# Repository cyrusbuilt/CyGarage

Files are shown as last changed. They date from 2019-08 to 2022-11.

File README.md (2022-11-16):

# CyGarage



Arduino-based (specifically the Adafruit Huzzah ESP8266) IoT garage door opener.

The code in this repository represents the Firmware for the CyGarage IoT garage door opener device, as well as some components for integrating with [OpenHAB2](https://openhab.org).  CyGarage is a [PlatformIO](https://platformio.org/) project and is meant to integrate with an existing garage door opener and provide 2 things: The ability to detect the door's state (open, close, or ajar) and the ability to control the door over HTTP/MQTT. Since there is an [ESP8266](https://www.adafruit.com/product/2471) at the heart of it, that means it is WiFi-enabled and is capable of OTA (Over-the-Air) firmware updates.

## Important Note on Security

CyGarage firmware versions prior to v1.3 had no security built-in and used basic unencrypted HTTP requests for control. There was no SSL (HTTPS) or authentication of any kind. This was a major concern because if someone opened access to the device through their firewall or if a malicious actor were to gain access to the WiFi LAN the device was attached to, being able to open the garage door was trivial. Simply send an HTTP POST to the activation URL and the door opens.  However, starting in v1.3, the default is to use [MQTT](http://mqtt.org/) to pass control messages in JSON format and in turn the device sends status messages in JSON format to MQTT subscribers (such as OpenHAB2). Additionally, these messages are transferred to/from MQTT over TLS using SSL certificates so that the messages are encrypted.  You cannot send control messages to CyGarage directly. You have to publish them to the control channel on the MQTT broker that CyGarage is subscribed to. Additionally, you would need the appropriate certificate and SHA256 fingerprint to connect to and publish the control messages. This security architecture is certainly not infalible, but definitely adds a strong layer of security that was non-existent in previous versions and also provides some means of hardening that security even further (such as using certificates signed by an RSA CA (as opposed to self-signed certs) and using password authentication with the MQTT broker on top of that. You can even configure OpenHAB2 to communicate with the MQTT broker using TLS as well, although this is overkill if the broker is running on the same machine as OpenHAB2 and/or the MQTT standard port is bound to the OpenHAB2 host).

## Theory of Operation

The way this is intended to work is: when the device detects that the door is open or ajar, the user can see this status and (if integrated with OpenHAB or some other similar system) and can get notifications when this occurs. When the device receives the activate command, it then triggers a relay which simulates the garage door button press which will in turn raise or lower the door depending on the current state.  Door activation is essentially "fire-and-forget". It will activate the relay and then assume that the garage door is working. CyGarage then monitors door state using the 2 sensor inputs. It is important to understand this system is not intended to replace the controller inside the garage door opener, but instead *compliments* it by adding state monitoring and remote activation.  Safety checks (something in the path of the door when closing) should still be handled by the garage door opener itself, for example.

## Configuration

The config.h file contains default configuration directives. These options are the hardcoded default values that the system will initially boot with. However, if there is a config.json file present in the root of the SPIFFS file system, then it will override these defaults. Here we'll discuss each option:

- CG_MODEL_2: Comment this line if you are building the firmware for the Model 1 (single door version). By default, this firmare supports Model 2.
- ENABLE_OTA: If you do not wish to support OTA updates, just comment this define.
- ENABLE_MDNS: If you do not wish to support [MDNS](https://tttapa.github.io/ESP8266/Chap08%20-%20mDNS.html), comment this define.
- ENABLE_WEBSERVER: This option is disabled by default for security reasons. Only uncomment this line if you know what you are doing or if you absolutely need it for backward compatibility with older versions of CyGarageMobile.
- CONFIG_FILE_PATH: This is the path to the configuration file. The default is /config.json. The values in this file will override these defaults.
- DEFAULT_SSID: Change this line to reflect the SSID of your WiFi network.
- DEFAULT_PASSWORD: Change this line to reflect the password to your WiFi network.
- WEBSERVER_PORT: If you wish to use a port number other than the standard HTTP port, you can change that here. This option is ignored if ENABLE_WEBSERVER is disabled.
- CLOCK_TIMEZONE: The GMT offset for your timezone (EST [America/New York] is -4 when observing DST. It's -5 when not.)
- SERIAL_BAUD: While it is not recommended, you can change the BAUD rate of the serial port here.
- CHECK_WIFI_INTERVAL: The interval (in milliseconds) to check to make sure the device is still connected to WiFi, and if not attempt to reconnect. Default is 30 seconds.
- CHECK_SENSORS_INTERVAL: The interval (in millisceonds) to check the door contact sensors to determine door state. Default is 3 seconds.
- CLOCK_SYNC_INTERVAL: The interval (in milliseconds) to try to resync the clock with NTP. Default is 1 hour.
- ACTIVATION_DURATION: The amount of time (in milliseconds) to activate the door relay. Default is 2.5 seconds and is recommended this value not be changed unless you have good reason for doing so.
- DEVICE_NAME: This essentially serves as the host name of the device on the network.
- CHECK_MQTT_INTERVAL: The interval (in milliseconds) to check connectivity to the MQTT broker. If the connection is lost, a reconnect will occur. The default value is 35 seconds.
- MQTT_TOPIC_STATUS: The MQTT status topic to publish device status messages to. Default is 'cygarage/status'.
- MQTT_TOPIC_CONTROL: The MQTT control topic to subscribe to for control messages. Default is 'cygarage/control'.
- MQTT_BROKER: The hostname or IP of the MQTT broker.
- MQTT_PORT: The port on the MQTT broker to connect to. The default is 8883 (default port for MQTT over TLS).
- OTA_HOST_PORT: Defines the port to listen for OTA updates on. This option is ignored if ENABLE_OTA is disabled.
- OTA_PASSWORD: The password used to authenticate with the OTA server. This option is ignored if ENABLE_OTA is disabled.
- ip: The default IP address. By default, this devices boots with a static IP configuration. The default IP is 192.168.0.200. You can change that here if you wish.
- gw: The default gateway address. The current default is 192.168.0.1. You can change that here if you wish.
- sm: The subnet mask. By default, it is 255.255.255.0, but you can change that here if need be.

To override the default configuration options, you need to upload a filesystem image containing a file named 'config.json' in the root of the SPIFFS filesystem. The file should like something like this:

```json
{
    "hostname": "CYGARAGE",
    "useDHCP": false,
    "ip": "your_device_ip_here",
    "gateway": "your_gateway_here",
    "subnetMask": "your_subnet_mask_here",
    "wifiSSID": "your_wifi_SSID_here",
    "wifiPassword": "your_wifi_password_here",
    "webserverPort": 80,
    "otaPort": 8266,
    "otaPassword": "your_OTA_password_here",
    "mqttBroker": "your_MQTT_broker_here",
    "mqttPort": 8883,
    "mqttControlChannel": "cygarage/control",
    "mqttStatusChannel": "cygarage/status",
    "mqttUsername": "your_mqtt_username_here",
    "mqttPassword": "your_mqtt_password_here",
    "serverFingerprintPath": "/mqtt.fpn",
    "caCertificatePath": "/ca.crt"
}
```

This configuration file is pretty self explanatory and one is included in the source. The file *MUST* be located in the "data" directory located in the root of the project in order to be picked up by the flash uploader (either via Serial or OTA). Each of the options in the configuration file are self-explanatory and match up with the hard-coded default settings mentioned above. If this file is not present when the firmware boots, a new file will be created and populated with the hardcoded defaults. These defaults can then be changed via the fail-safe menu and saved. You'll notice a couple of additional options in the config.json file not present in config.h. They are as follows:

- mqttUsername: If you have enabled password authentication on your MQTT broker, provide the username here.
- mqttPassword: If you have enabled password authentication on your MQTT broker, provide the password for the username above. If *both* the username and password are provided, then CyGarage will attempt to connect to the broker with the provided credentials; Otherwise, it will attempt to connect without credentials.
- mqttControlChannel: The MQTT control topic to subscribe to in order to receive device commands.
- mqttStatusChannel: The MQTT status topic to publish device status to.
- serverFingerprintPath: The path to the file containing the MQTT broker's SHA256 fingerprint. Default is '/mqtt.fpn'.
- caCertificatePath: The path to the CA certificate that the MQTT broker's certificate was signed with. Default is '/ca.crt'.

If the above values are omitted or invalid, then the system will fail during loadCertificates() and will not be able to connect to MQTT.

## Startup Configuration Sequence

During the boot sequence, configuration defaults are loaded from the directives in config.h. If the config.json file is present at boot, then any configuration values found in there will override the default values in memory.  If no config.json file is found or if it could not be read, then the system will continue using the default values and then generate a new config.json file and populate it with the default values that were loaded. Upon subsequent boots, these values can then be read from config.json and altered by the user. When configuration changes are made from the CLI, the altered values take effect immediately, but are only stored in memory unless the users chooses to save the configuration. Otherwise, all in-memory configuration changes are lost upon reboot (intentionally) so that the user can fallback to a known-good state they entered bad configuration data.

## Getting Started

After you've configured everything the way you need it (as discussed above), build the firmware by either clicking "Build" in the PlatformIO tasks menu, or by opening a terminal to the project directory and typing:

```bash
> platformio run
```

NOTE: The first time you flash the Huzzah, you need to do so over serial (since the OTA code isn't there yet), but subsequent uploads can be done via OTA if configured properly.

The next thing to do is connect the Huzzah to your computer using an FTDI cable like [this one](https://www.adafruit.com/product/70?gclid=EAIaIQobChMIm7-50ZiZ5AIVlIvICh284QPxEAQYBCABEgJkcPD_BwE) and then configure the port in platformio.ini like so:

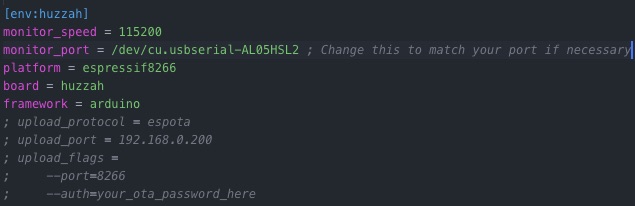
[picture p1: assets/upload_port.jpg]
config


With the above mentioned FTDI cable attached to my MacBook, the port appears as it does in the config file above (usually PlatformIO is pretty good about auto-detecting the port for you).

Now all you have to do is flash the firmware onto the Huzzah. You can do this by first pressing and holding the "GPIO" button and then press the "reset" button and let go of both on the Huzzah to put it into flash mode (this is not necessary when you flash via OTA), then click the "Upload and Monitor" task in the PlatformIO menu or by typing the following into the terminal:

```bash
> platformio run --target upload
> platformio device monitor --baud 115200 --port /dev/cu.usbserial-AL05HSL2
```

Once complete, press the "reset" button on the Huzzah. You should see the device boot up in the serial console. Now put the device back into flash mode. If you are using MQTT over TLS (recommended) then visit the readme in the "openhab" folder (even if you ultimately are not connecting MQTT to OpenHAB) for instructions on generating the necessary files for connecting CyGarage to MQTT, otherwise just click the "Upload File System Image" task in the PlatformIO menu. When finished, press the "reset" button again and the device will reboot and come back up with your new configuration settings.

## Webserver Routes (Deprecated)

These routes are *ONLY* exposed if the ENABLE_WEBSERVER directive is uncommented.

- GET /    (Returns "Server ok..." in plain text)
- GET /version (Returns the firmware version in plain text)
- GET /device/status (Returns the device (door) status in plain text)
- POST /device/activate (Activates the relay and returns "OK" in plain text)

## OTA Updates

If you wish to be able to upload firmware updates Over-the-Air, then besides leaving the ENABLE_OTA option uncommented, you will also need to uncomment all the upload_* lines in platformio.ini, and change the line 'upload_port = ' line to reflect the IP of the device and the line '--auth=' to reflect whatever OTA_PASSWORD is set to. Then when you click "upload" from the PlatformIO tasks (or if you execute 'platformio run --target upload' from the command line) it should upload directly over WiFi and once completed, the device will automatically flash itself and reboot with the new version. If you wish to upload a new configuration file, you can also do this via OTA. Assuming the above-mentioned settings are configured, you can then click "Upload File System Image" from the PlatformIO project tasks.

## Serial Console Menu

If the device ever fails to connect to WiFi or if you press the 'I' key on your keyboard while in the serial console, normal operation of the device is suspended and the device will fall into a 'fail-safe' mode and present the user with a command menu. Here we will discuss those menu options:

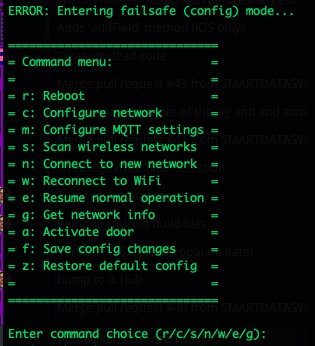
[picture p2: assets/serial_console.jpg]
Console Menu


- Reboot - press 'r' - Self-explanatory. Reboots the device.
- Configure network - press 'c'. Configure the network.

- - Press 'd' for DHCP or 't' for static IP.

- - If static, then you will also be prompted for the IP, gateway, and subnet mask.

- Scan wireless networks - Press 's'. This will scan for available wireless networks and dump a table of the networks it found to the console.

- Connect to new network - Press 'n'. This option prompts the user for a new SSID and password for different WiFi network to connect to.

- Reconnect to WiFi - Press 'w'. This can be used to reconnect to the current WiFi network if the connection was lost.

- Resume normal operation - Press 'e'. This will leave fail-safe mode and attempt to resume normal operation by resuming any suspended tasks and verify network connectivity.

- Get network info - Press 'g'. This will dump network information to the serial console (IP config, WiFi connection info).

- Activate door (1) - Press 'a'. This allows the user to manually activate the door. Activates door 1 on Model 2.

- Activate door 2 - Press 'b'. This allows the user to manually activate door 2. Not present on Model 1 firmware.

- Save config changes - Press 'f'. This will save any configuration changes currently stored in memory to config.json.

- Restore default config - Press 'z'. This will restore the firmware configuration back to the factory default settings (the hard-coded defaults). It does this by simply deleting the existing config.json file from flash storage and then immediately rebooting the firmware. Upon reboot, a new config.json file is created and populated with the default settings which are then applied to the running configuration in memory.

## Dependencies

The firmware dependencies will be installed automatically at compile-time.  However, if you wish to install dependencies prior to compiling (for intellisense or to clear warnings/errors in the VSCode editor) you can run the following command:

```bash
platformio lib install
```

Then go to the platformio menu and click "Rebuild IntelliSense index".

## Tools

Included with this firmware is a few handy tools:

- /disassemble.sh - Disassembles the compiled firmware into a plain text file called 'disassembly.txt'. If the firmware has not been built, it will be compiled first, then disassembled. The disassembly output contains the assembly code, C++ calls, and instruction addresses useful for debugging the executing code or determining the cause of crashes at addresses reported by ESPCrashMonitor during boot.

- tools/clear_flash.sh - Completely clears the flash memory on the ESP8266 of all data (including firmware).

- tools/serial_monitor.sh - Just runs the serial monitor. Pretty much the same as clicking 'Monitor' in the platformio menu, but uses its own settings instead of those found in platformio.ini.

- tools/generate_mqtt_certs.sh - Generates the necessary certificates for the MQTT broker and CyGarage to communicate over TLS.

## Mobile App

If you choose not to integrate with OpenHAB2, you can get similar functionality using the mobile app for iOS and Android located [here](https://github.com/cyrusbuilt/CyGarageMobile). (NOTE: As of 8/21/2019, the most current version of CyGarageMobile is only compatible with CyGarage firmware version prior to v1.3, or if the ENABLE_WEBSERVER option is enabled in v1.3 or higher). If you intend to integrate with OpenHAB2, you can also use the OpenHAB mobile application (recommended).

## Integration with Garage Door opener

Once the board is assembled (either by having the board etched or by just soldering the necessary components to perf board and making the connections manually), you will need to mount the board somewhere and then make the necessary connections to the opener. If using door contacts is not an option for you (which was the case for me), it is possible to use the limit switches already mounted to the track to tell the motor to stop when the door is all the way open or all the way closed. Many garage door openers have voltage present on these limit switches. In the case of my Genie, there was 7.7V DC present when the limit switches were open, which then goes to 0V when the switches closed. We can't have that voltage (or current) being fed back in to the inputs on the ESP8266, so rectifier diodes (D1 and D2) were added to the circuit just before J2 and J3 (respectively). This allows us to use the existing switches, but still isolate the ESP8266 from the garage door opener's voltage and prevent ground loops. That being said, the first thing to do is to locate the terminals on the garage door opener that the wall-mounted push button wires to.

*MOST* garage door openers have a button mounted near the interior door that you can press to open/close the garage door. Follow the wires from that button and see which terminals they wire into on the opener. You need to connect 2 wires from the push button terminals on the opener to the COM and NO screw terminals on the Power Relay FeatherWing (I ran appropriate lengths of 18/2 (18 Guage / 2 lead) for all my connections and mounted the CyGarage board on the wall where I could easily get to it). Next, connect 2 wires each to J2 and J3 and then connect the other ends of each to either magnetic door contacts or the limit switches mounted on the trolley track.  If connecting to the limit switches, it is important to be sure that you are connecting the outside terminals (think of these as the negative or ground terminals) to the frame or ground on the track itself and the inside terminals (think of these as the positive terminals) to the switch leads themselves.

Last, you need to connect a 5VDC 1A power supply to J1. I personally used a power adapter for an old USB hub I still had laying around. But a lot of cell phone chargers and the like would work too, or the 5VDC rail from an old PC power supply, or you could build one, which wouldn't be that difficult. If you intend to mount the board somewhere that will be difficult to hook up to a computer later, it would be best to make sure you flash the ESP8266 with the firmware first. Since mine was mounted on the wall near one of my benches, I just set my laptop on the bench and connect the USB-to-Serial cable and flash it right there (when necessary, I mostly just use the OTA feature). I would HIGHLY recommend that you use female headers to create a sort of 'socket' for the Huzzah. That way it can be replaced if something happens or so you can pop it out and flash it if needed.

For Model 2:

The same as above except J3 and J4 connect to door contacts or limit switches on door 2, and relay 2 connects to the push button terminals on the opener for door 2.

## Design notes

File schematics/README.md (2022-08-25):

# CyGarage Schematics

All files were produced using [EasyEDA](https://easyeda.com/). The following is a list of files and what they are:

- Model1-Single-Door/COM_CyGarage.csv - The bill of materials in CSV format.

- Model1-Single-Door/PCB_CyGarage.pdf - A PDF version of the PCB view.

- Model1-Single-Door/SCH_CyGarage.pdf - A PDF version of the schematic view.

- Model1-Single-Door/PCB_CyGarage.json - The original EasyEDA CAD file of the schematic.

- Model1-Single-Door/SCH_CyGarage.json - The original EasyEDA CAD file of the PCB.

- Model1-Single-Door/gerber - Exported Gerber files useful for importing into other CAD programs or for sending to fab houses that do not support Easy EDA files.

- Model2-Dual-Door/* - Contains all of the same things, but for the 2 door model.

## NOTES

DC1 and DC2 (and DC3 and DC4 for Model2) are actually intended to connect to the limit switches on the garage door track. These are used for sensing door position.

The power supply used is a 5VDC 1A supply which connects to JP1.

When DC1 (connected to JP2) closes, the controller will consider the door to be in the 'open' state. This is the limit switch on the near-end of the trolley track (closest to the opener). When this switch is closed, the garage door opener stops because the door should be fully opened.

When DC2 (connected to JP3) closes the controller will consider the door to be in the 'closed' state (unless DC1 is also closed, which should never happen). This is the limit switch on the far-end of the trolley track (closest to the garage door). When this switch is closed, the garage door opener stops because the door should be fully closed. When both switches are opened, the door is considered to be "ajar".

The OPENER terminals should connect to the button terminals on the garage door opener. When the relay activates, these will be connected for approx. 2.5 seconds and then open again, thus simulating a momentary button press which should in turn activate the garage door opener.

Additionally, I opted to use female stacking headers where the pins of the ESP8266 should go (creating a "socket" of sorts) to allow the module to be removable. This is optional, but handy in the event that the module ever becomes damaged or if the EEPROM wears out, or something of that nature, it can be easily replaced.

DC1 and DC2 (and DC3 and DC4 for Model2) can also be connected to door contacts if using on a garage door that doesn't use limit switches (such as automatic industrial overhead door openers).

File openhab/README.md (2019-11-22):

# OpenHAB Components

This directory contains components for integrating with OpenHAB2.

## Instructions for integrating with OpenHAB2

The first thing you will need to do if you haven't already, is install an MQTT broker. For the purposes of this guide, I will assume you will be using [Mosquitto](https://mosquitto.org/) and will be installing it on the same machine as OpenHAB2.

To install mosquitto, follow the download and install instructions [here](https://mosquitto.org/download/). But assuming you are installing on an Ubuntu or Ubuntu-based system just run:

```bash
> sudo apt-add-repository ppa:mosquitto-dev/mosquitto-ppa
> sudo apt-get update
> sudo apt install mosquitto mosquitto-clients
```

Next we need to generate the necessary SSL certificates that will be used for communication over TLS.  There is a shell script in the tools directory that simplifies this process. Just run:

```bash
> tools/./generate_mqtt_certs.sh
```

You will first be prompted for the hostname and IP address of your MQTT broker (in this example, it is the same as the your OpenHAB2 server). It will also prompt you for some additional information such as country, state/province, Organizational Unit, org name, etc. It will also prompt you for a password. Make note of this password. When the script is finished it will output a bunch of files in tools/certs. As the script indicates, the ones we are most interested in are host_name.key.pem, hostname_.crt.pem, and ca.crt.pem (where host_name is the host name you provided when the tool first ran). These 3 files need to be copied somewhere on your MQTT server. For this example let's assume /etc/mosquitto/certs.

```bash
> sudo mkdir /etc/mosquitto/certs
> sudo cp -f tools/certs/host_name.key.pem /etc/mosquitto/certs
> sudo cp -f tools/certs/host_name.crt.pem /etc/mosquitto/certs
> sudo cp -f tools/certs/ca.crt.pem /etc/mosquitto/certs
```

Next, we need to configure it.

```bash
> sudo nano /etc/mosquitto/mosquitto.conf
```

First make sure the following line is present:

```txt
listener 1883 localhost
```

This binds port 1883 (the default non-SSL port) for MQTT to only allow traffic from the local host.  This is done because encrypting the traffic between OH2 and MQTT when they are running on the same host is overkill, but we also need to make sure that *ONLY* the localhost can do this.  All other traffic will then have to go through another port. In our case, 'all other traffic' will be encrypted traffic. This means we need to define another port and supply the certificates like so:

```txt
listener 1883 localhost

listener 8883
cafile /etc/mosquitto/certs/ca.crt.pem
certfile /etc/mosquitto/certs/host_name.crt.pem
keyfile /etc/mosquitto/certs/host_name.key.pem
```

Press CTRL+X to save and close the file.  Now restart MQTT:

```bash
> sudo systemctl restart mosquitto.service
> sudo systemctl status mosquitto.service
```

It should start back up normally and show the status as active. Now lets test it out:

```bash
> mosquitto_sub -h localhost -p 1883 -t cygarage/status &
> mosquitto_pub -h localhost -p 1883 -t cygarage/status -m "{\"foo\":\"bar\"}"
{"foo":"bar"}
```

You should see the message output. Now you can kill the subscription you created with the first command:

```bash
> fg
```

Now press CTRL+C.

Next, we need to configure OpenHAB to use the MQTT broker. To do this, go to PaperUI -> Addons -> Bindings and install the MQTT Binding.  Once the installation is complete, we need to configure the service:

```bash
> sudo nano /etc/openhab2/services/mqtt.cfg
```

Add the following lines:

```txt
mqtt:localBroker.url=tcp://localhost:1883
mqtt:localBroker.clientId=openhab2
mqtt:localBroker.qos=0
```

Save and close the file.

## Optional password authentication

If you wish to use password authentication with Mosquitto, then there are some additional steps. First, you need to generate the password file.

```bash
> sudo mosquitto_passwd -c /etc/mosquitto/passwd cygarage
```

Where "cygarage" is the username. You can make this whatever you want as long as this same username is what you put in the CyGarage config and in the cygarage.things file. Next, we need to modify the mosquitto config again:

```bash
> sudo nano /etc/mosquitto/mosquitto.conf
```

And add the following lines to the file:

```txt
allow_anonymous false
password_file /etc/mosquitto/passwd
```

Save and close, then restart the service:

```bash
> sudo systemctl restart mosquitto.service
```

Next we need to copy the following files to the openhab-conf folder on the server:

## mqttbridge.things

This is a "Thing" definition for the MQTT bridge. This bridge can be used by anything else in OH2 that needs it. This simply defines a bridge to MQTT that registers OH2 as a client. If a Thing definition for this bridge already exists, no need to copy it again. If not, then copy this file to the openhab-conf/things directory.

## model1/cygarage.things

This is a "Thing" definition for CyGarage that binds the channels we need to MQTT.  You can edit the binding if needed, (such as adding the mosquitto username and password, hostname or IP and port) then copy this file to the openhab-conf/things directory.

## model1/cygarage.items

This file defines the items that will bind to the channels in the cygarage.things file, which will represent controls and display values. Copy this file to your openhab-conf/items folder.

## model1/cygarage.sitemap

This is the sitemap contains all the items defined in the cygarage.items file and makes up all the monitor and control items on one screen. Copy this file to your openhab-conf/sitemaps folder.

## model1/cygarage.rules

Contains automation logic. This file is responsible for sending push notifications if the door is open/ajar for 15 minutes or longer and handles the control actions. Copy this file to your openhab-conf/rules folder.

## model2/*

The same files as above, but to for the Model 2 (2 door version).

## All set

Now that everything is in place. You need to restart OH2:

```bash
> sudo systemctl restart openhab2.service
```

Now lets make sure the service started successfully:

```bash
> sudo systemctl status openhab2.service
```

The service should be active. So let's test it:

```bash
> mosquitto_pub -h localhost -p 1883 -t cygarage/status -m "{\"client_id\":\"test\",\"state\":\"CLOSED\",\"firmwareVersion\":\"1.3\",\"systemState\":0}"
```

Now if you navigate to BasicUI in OH2 and click the CyGarage sitemap, you should see the System ID is "test", Firmware version is "1.3", System State is "Booting 0" and Current position is "CLOSED".

CyGarage Sitemap (Web Version)

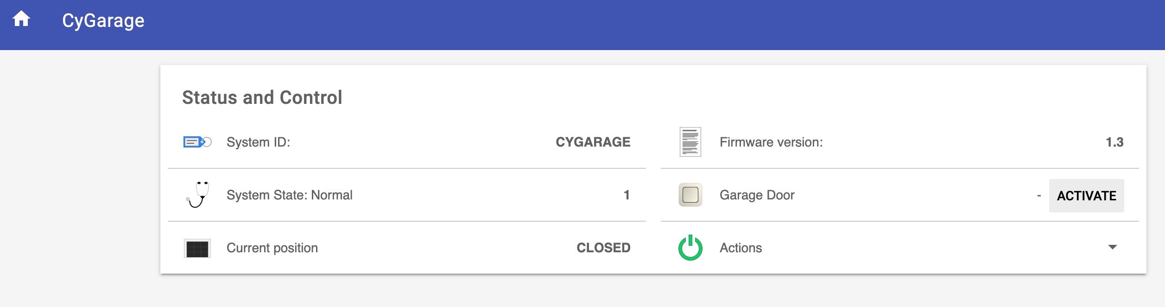
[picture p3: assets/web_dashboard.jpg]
Web Dashboard


CyGarage Sitemap (OH2 Mobile App Version)

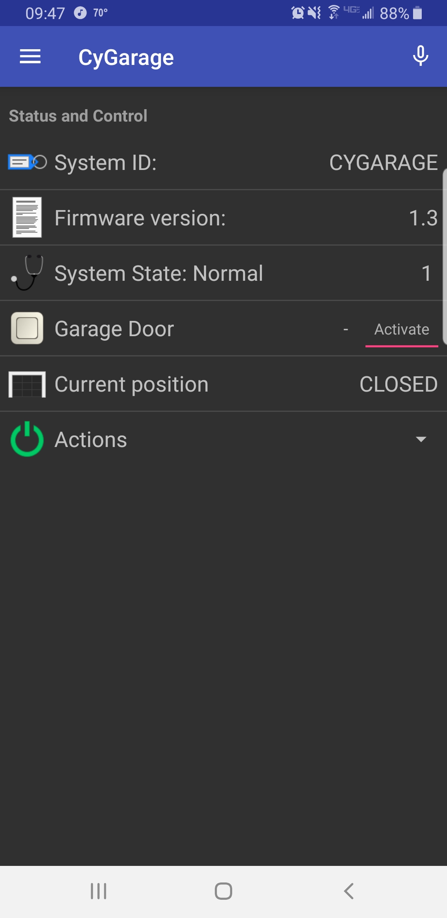
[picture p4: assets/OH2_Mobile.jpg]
Mobile Dashboard


## Dependencies

You will need the following dependent add-ons installed in OpenHAB2 for these components to work correctly:

[openHAB Cloud Connector](https://www.openhab.org/addons/integrations/openhabcloud/)

- You also need to connect your local OpenHAB server to a cloud instance in order to receive push notifications.

This is because cygarage.rules makes use of the sendBroadcastNotification() method which assumes you have linked your local OH2 server to a cloud OH2 instance, which can then make use of push notifications. If you do not wish to use push notifications or just don't want to link your local installation to a secure cloud instance, then don't install the cloud connector and comment out the necessary line cygarage.rules.

If all went well, you can now use CyGarage with your OH2 installation and control and monitor the garage door (securely) using the OH2 web console or via the OH2 mobile app.

## Finishing up

At this point the only thing left to do if you haven't already is to compile and upload the firmware (if you are happy with the defaults in config.h and your settings in config.json). Next make sure the device is operating normally and you can ping the IP of the device. You can even publish a command to the device to force it to report it's status back:

```bash
> mosquitto_pub -h localhost -p 1883 -t cygarage/control -m "{\"client_id\":\"CYGARAGE\",\"command\": 4}"
```

The 'data' directory in this project should now contain 3 files: config.json, ca.crt, and mqtt.fpn.

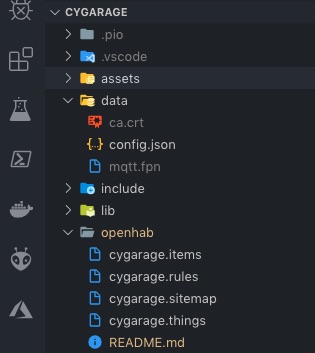
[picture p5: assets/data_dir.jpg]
Data Folder


If so, click "Upload File System image" from the PlatformIO tasks and it will upload those files to CyGarage and it will reboot when finished. Once it comes back up, it should be able to establish a connection to MQTT and you should see it's status in OH2.

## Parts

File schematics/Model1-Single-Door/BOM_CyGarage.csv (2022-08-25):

ID | Name | Designator | Footprint | Quantity | Manufacturer Part | Manufacturer | Supplier | Supplier Part | Price
1 | 5mm | D1,D6 | PKG-LED-5MM-RED | 2 | L-1503EC | KINGBRIGHT | Element14 | 1003201
2 | LED-GREEN-2.54-5mm | D2 | LED-GREEN-2.54-5MM-YUN | 1 | 503UOC
3 | 1N4001 | D3,D4,D5 | DIODE-1N4001 | 3
4 | Header-Male-2.54_1x6 | H1 | HEADER-MALE-2.54_1X6 | 1
5 | M023.5MM | JP1,JP2,JP3,JP4 | SCREWTERMINAL-3.5MM-2 | 4
6 | G5LE-14_DC3 | K1 | G5LE-14_SPDT | 1
7 | 330 | R1,R2 | RESISTOR 1/4 WATT 330 OHM | 2
8 | 150 | R3 | RESISTOR 1/4 WATT 150 OHM | 1
9 | Huzzah ESP8266 Breakout_TT | U1 | HUZZAH 8266 | 1 |  | Adafruit

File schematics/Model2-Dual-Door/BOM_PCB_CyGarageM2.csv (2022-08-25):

ID | Name | Designator | Footprint | Quantity | Manufacturer Part | Manufacturer | Supplier | Supplier Part | Price
1 | 5mm | D1,D6 | PKG-LED-5MM-RED | 2 | L-1503EC | KINGBRIGHT | Element14 | 1003201
2 | LED-GREEN-2.54-5mm | D2 | LED-GREEN-2.54-5MM-YUN | 1 | 503UOC
3 | 1N4001 | D3,D4,D5,D7,D8,D9 | DIODE-1N4001 | 6
4 | Header-Male-2.54_1x6 | H1 | HEADER-MALE-2.54_1X6 | 1
5 | M023.5MM | JP1,JP2,JP3,JP4,JP5,JP6,JP7 | SCREWTERMINAL-3.5MM-2 | 7
6 | G5LE-14_DC3 | K1,K2 | G5LE-14_SPDT | 2
7 | 330 | R1,R2,R4,R5 | RESISTOR 1/4 WATT 330 OHM | 4
8 | 150 | R3 | RESISTOR 1/4 WATT 150 OHM | 1
9 | Huzzah ESP8266 Breakout_TT | U1 | HUZZAH 8266 | 1 |  | Adafruit

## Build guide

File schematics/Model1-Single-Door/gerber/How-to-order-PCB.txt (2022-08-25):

How to Order PCB

Please refer to:
https://docs.easyeda.com/en/PCB/Order-PCB

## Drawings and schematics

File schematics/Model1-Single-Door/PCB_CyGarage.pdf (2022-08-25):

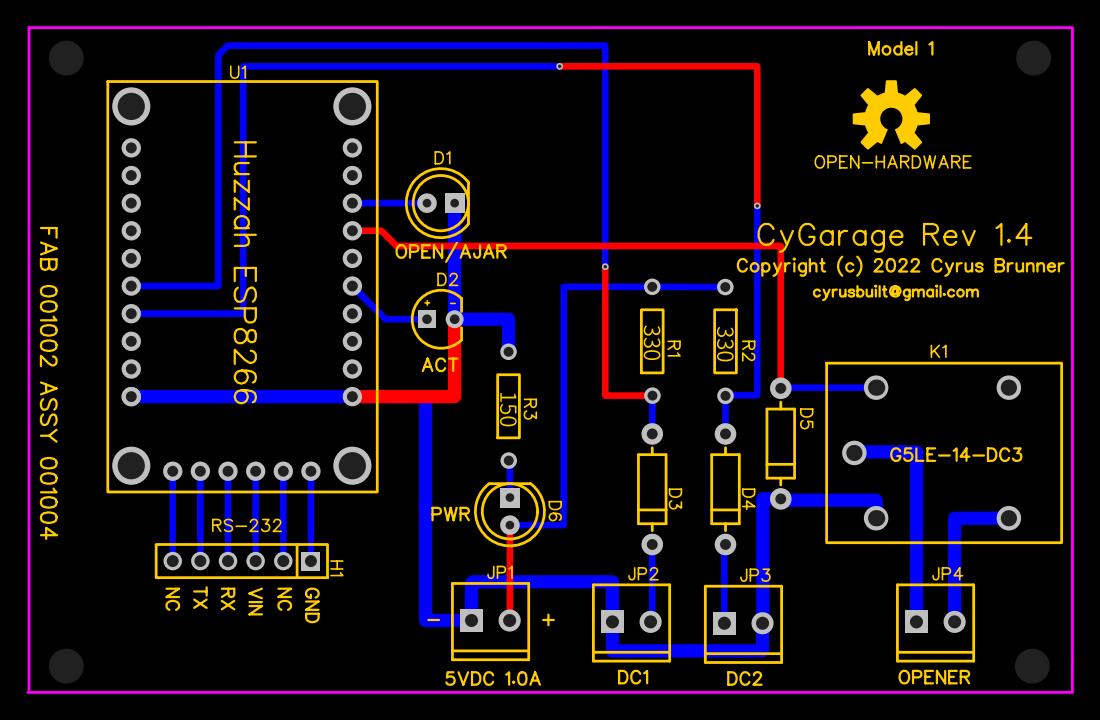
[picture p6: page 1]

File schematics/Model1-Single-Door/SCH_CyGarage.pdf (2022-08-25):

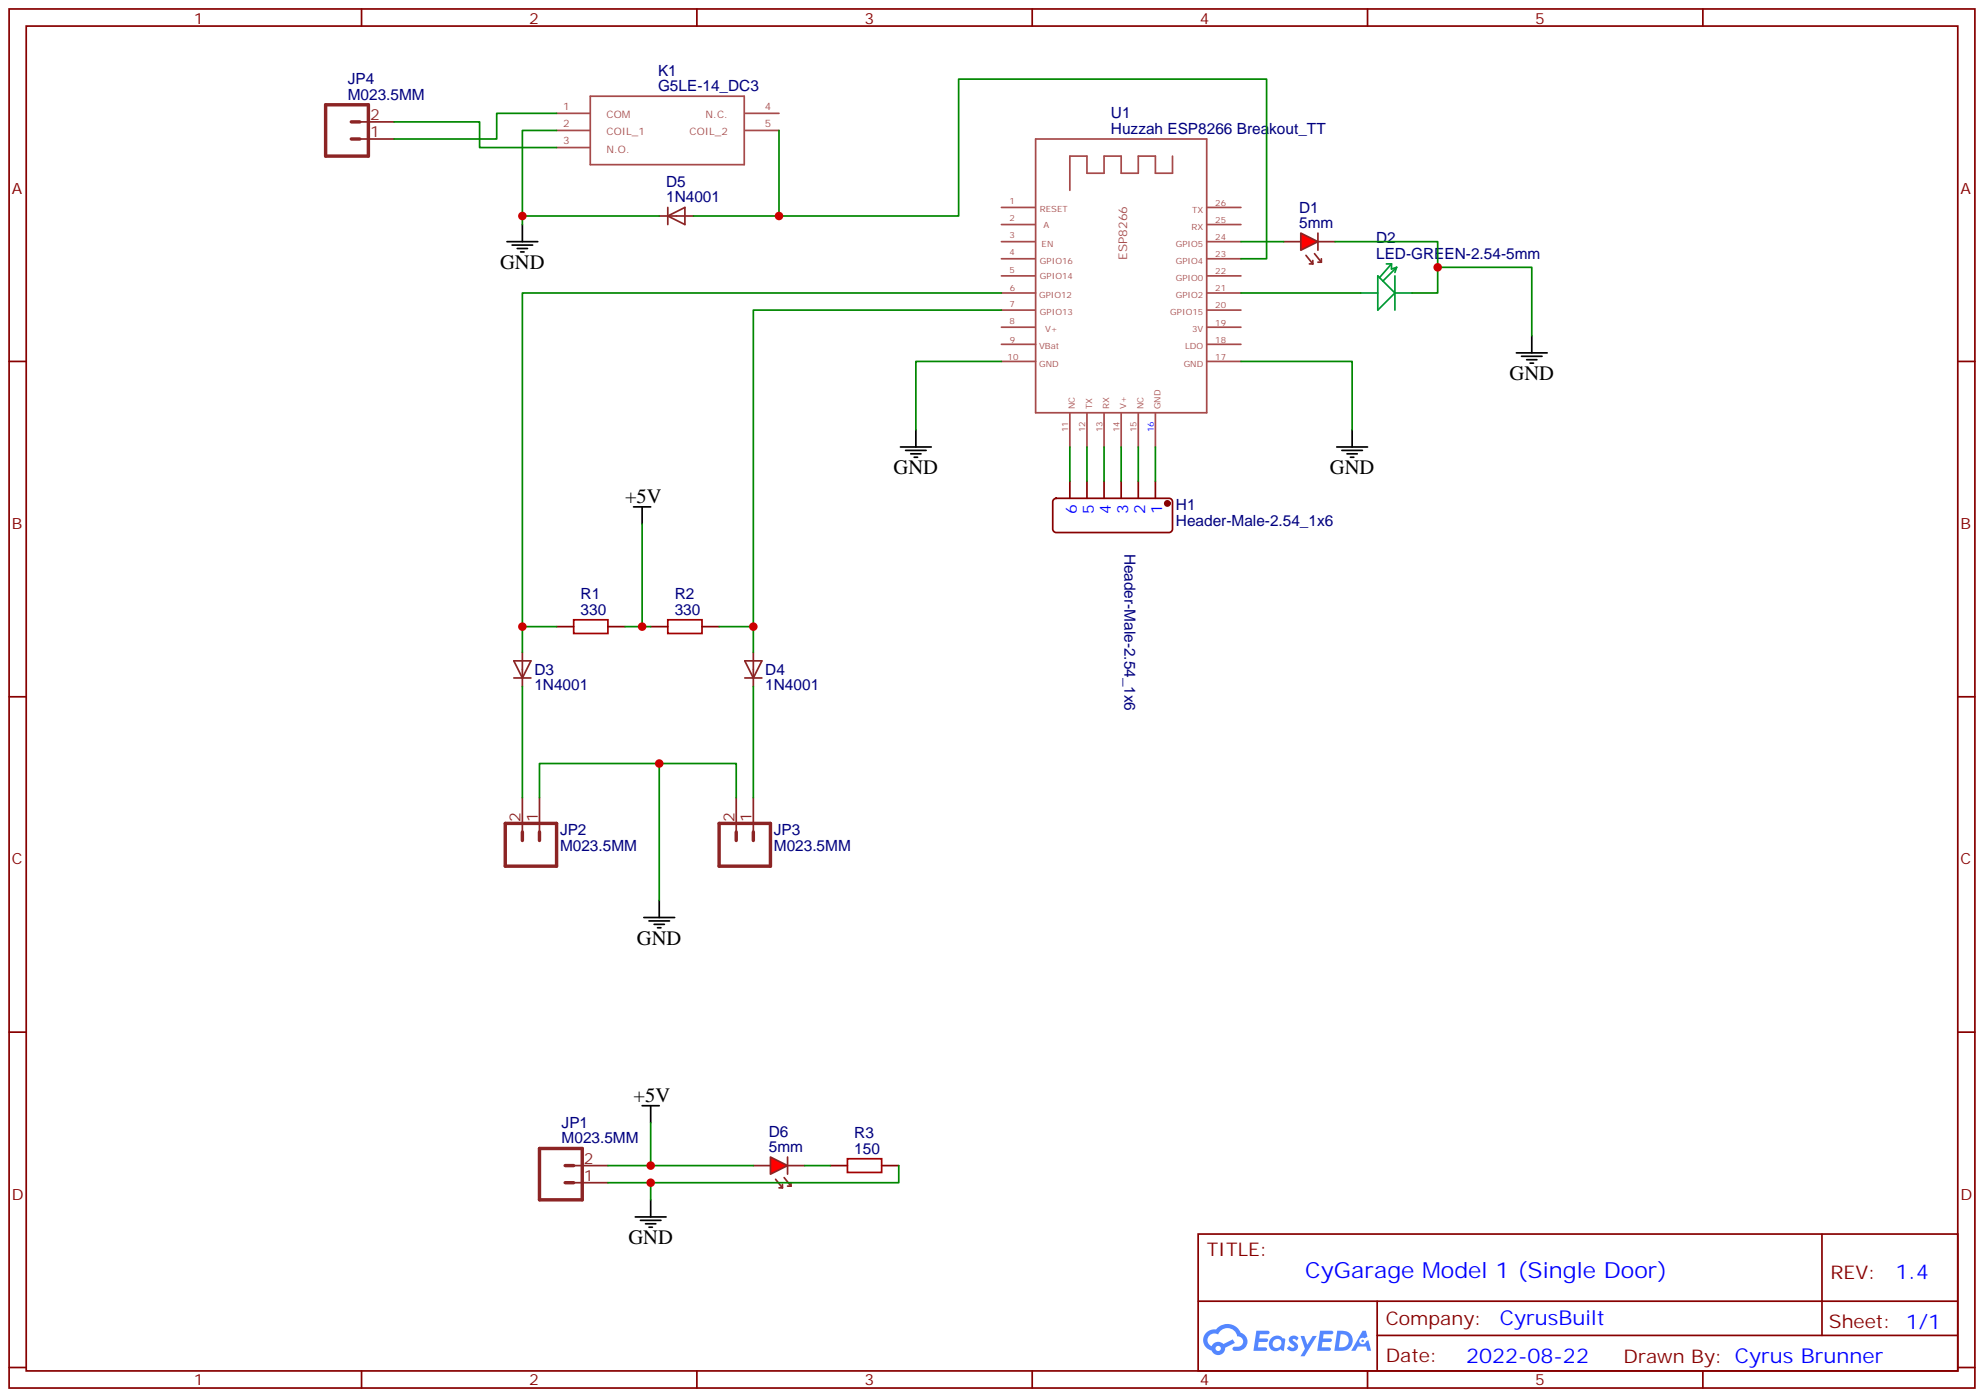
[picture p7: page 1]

Drawn By: Cyrus Brunner

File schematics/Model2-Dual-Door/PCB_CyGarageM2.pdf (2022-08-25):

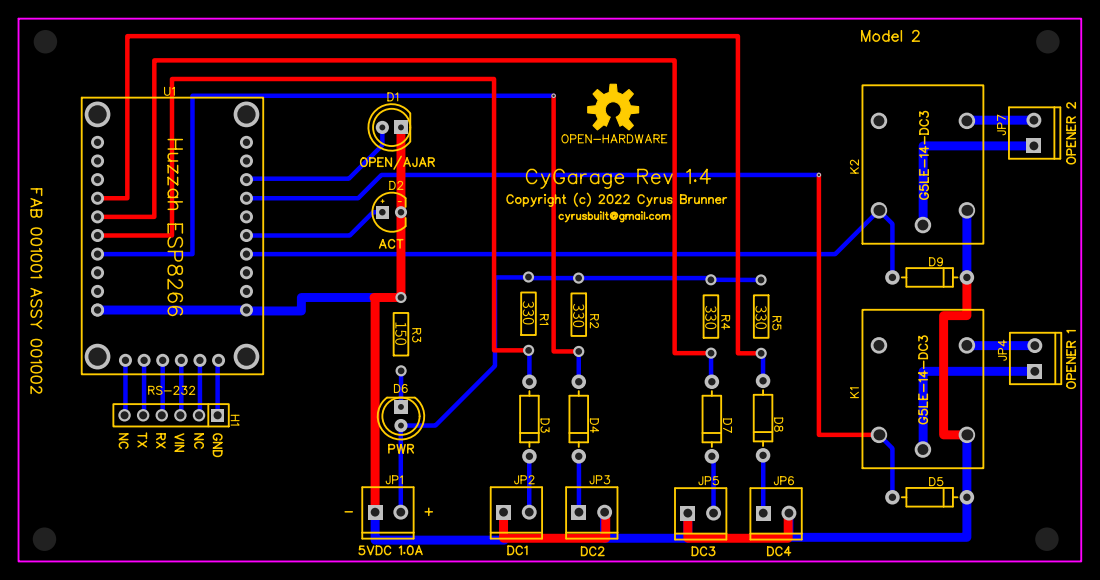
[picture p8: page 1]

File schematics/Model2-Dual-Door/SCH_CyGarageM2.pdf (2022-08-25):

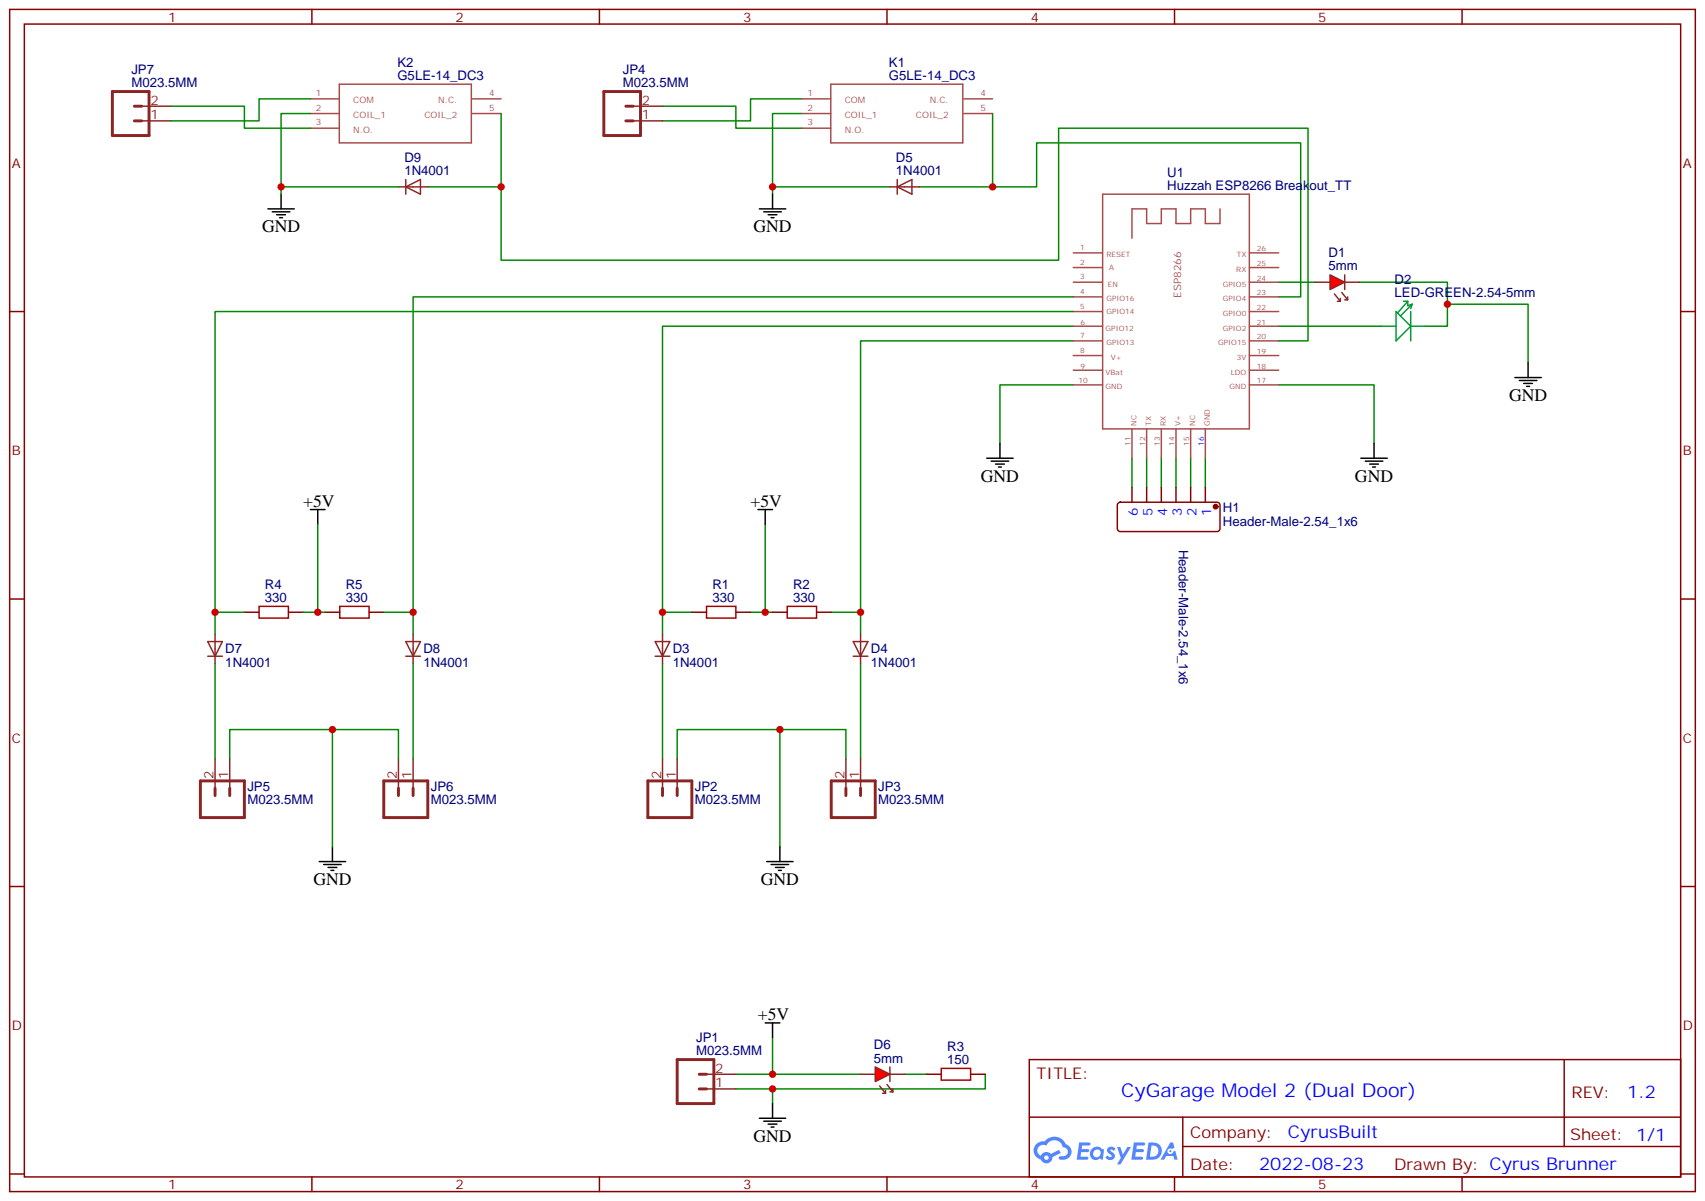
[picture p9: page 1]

Drawn By: Cyrus Brunner

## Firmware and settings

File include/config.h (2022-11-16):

/**
 * config.h
 * CyGarage v2.2
 * 
 * (c) 2019,2020, Cyrus Brunner
 * 
 * This file provides default configuration values. Some of these values can
 * be overridden using a configuration file called 'config.json' in the root
 * of the SPIFFS filesystem. If configuration file cannot be found, cannot be
 * loaded, or does not contain certain configuration values, then these values
 * will be used instead.
 */

#ifndef config_h
#define config_h

#include <IPAddress.h>

// Configuration
//#define CG_MODEL_2                            // Comment this line to revert to Model 1 (single door) firmware.
#define DEVICE_NAME "CYGARAGE"                  // The device name.
#define DEVICE_CLASS "cygarage"                 // The device class (used for discovery).
#define ENABLE_OTA                              // Comment this line to disable OTA updates.
#define ENABLE_MDNS                             // Comment this line to disable the MDNS.
#define CONFIG_FILE_PATH "/config.json"         // The config file path. Do not alter unless you are sure.
#define DEFAULT_SSID "your_ssid_here"           // Put the SSID of your WiFi here.
#define DEFAULT_PASSWORD "your_wifi_password"   // Put your WiFi password here.
#define CLOCK_TIMEZONE -4                       // The timezone this device is located in. (For example, EST when observing DST = GMT-4, when not = GMT-5)
#define SERIAL_BAUD 115200                      // The BAUD rate (speed) of the serial port (console).
#define CHECK_WIFI_INTERVAL 30000               // How often to check WiFi status (milliseconds).
#define CHECK_SENSORS_INTERVAL 3000             // How often to check sensors (milliseconds).
#define CLOCK_SYNC_INTERVAL 3600000             // How often to sync the local clock with NTP (milliseconds).
#define ACTIVATION_DURATION 2500                // How long the activation relay should be on.
#define CHECK_MQTT_INTERVAL 35000               // MQTT connectivity check interval (milliseconds).
#define MQTT_TOPIC_STATUS "cygarage/status"     // MQTT status topic to publish to.
#define MQTT_TOPIC_CONTROL "cygarage/control"   // MQTT control topic to subscribe to.
#define MQTT_TOPIC_DISCOVERY "redqueen/config"  // MQTT discovery topic to publish to.
#define MQTT_BROKER "your_mqtt_broker_IP"       // MQTT broker hostname or IP.
#define MQTT_PORT 8883                          // MQTT port number.
#ifdef ENABLE_OTA
    #include <ArduinoOTA.h>
    #define OTA_HOST_PORT 8266                         // The OTA updater port.
    #define OTA_PASSWORD "your_OTA_password_here"      // The OTA updater password.
#endif
IPAddress defaultIp(192, 168, 0, 200);                 // The default static host IP.
IPAddress defaultGw(192, 168, 0, 1);                   // The default static gateway IP.
IPAddress defaultSm(255, 255, 255, 0);                 // The default static subnet mask.
IPAddress defaultDns(defaultGw);                       // The default static DNS server IP (same as gateway for most residential setups)

typedef struct {
    // Network stuff
    String hostname;
    String ssid;
    String password;
    IPAddress ip;
    IPAddress gw;
    IPAddress sm;
    IPAddress dns;
    bool useDhcp;

    uint8_t clockTimezone;

    // MQTT stuff
    String mqttTopicStatus;
    String mqttTopicControl;
    String mqttTopicDiscovery;
    String mqttBroker;
    String mqttUsername;
    String mqttPassword;
    uint16_t mqttPort;

    // OTA stuff
    uint16_t otaPort;
    String otaPassword;
} config_t;

#endif

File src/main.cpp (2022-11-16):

/**
 * @file main.cpp
 * @author Chris "Cyrus" Brunner (cyrusbuilt at gmail dot com)
 * @brief  This is the firmware for CyGarage, an IoT garage door opener add-on. The device is intended
 * to integrate with an existing garage door opener and connect via WiFi, providing the ability
 * to sense when the door is open/closed/ajar and provide a means of opening/closing the door.
 * This firmware also allows for OTA firmware updates, and additionally can be integrated with
 * a home automation server such as OpenHAB.
 * @version 2.3
 * @date 2022-11-15
 * 
 * @copyright Copyright (c) 2022 Cyrus Brunner
 */

#ifndef ESP8266
    #error This firmware is only compatible with ESP8266 controllers.
#endif
#include <Arduino.h>
#include <ESP8266WiFi.h>
#include <WiFiClient.h>
#include <FS.h>
#include <time.h>
#include <TZ.h>
#include "DoorContact.h"
#include "LED.h"
#include "Relay.h"
#include "TaskScheduler.h"
#include "ResetManager.h"
#include "ESPCrashMonitor.h"
#include "ArduinoJson.h"
#include "PubSubClient.h"
#include "config.h"
#include "TelemetryHelper.h"
#include "Console.h"

#define FIRMWARE_VERSION "2.3"

// Startup delay before processing MQTT messages.
#define MQTT_STARTUP_DELAY 5000

// Pin definitions
#define PIN_SENSOR_LED 5
#define PIN_WIFI_LED 2
#define PIN_ACTIVATE 4
#define PIN_OPEN_SENSOR 12
#define PIN_CLOSE_SENSOR 13
#ifdef CG_MODEL_2
    #define PIN_OPEN_SENSOR_2 14
    #define PIN_CLOSE_SENSOR_2 16
    #define PIN_ACTIVATE_2 15
#endif

// Forward declarations
void onDoorContactStateChange(DoorInfo* sender);
void onCheckWiFi();
void onCheckActivation();
void failSafe();
void onCheckMqtt();
void onMqttMessage(char* topic, byte* payload, unsigned int length);
void onSyncClock();
void onEnableMqtt();

// Global vars
#ifdef ENABLE_MDNS
    #include <ESP8266mDNS.h>
    MDNSResponder mdns;
#endif
WiFiClient wifiClient;
PubSubClient mqttClient(wifiClient);
DoorContact openSensor(PIN_OPEN_SENSOR, onDoorContactStateChange);
DoorContact closeSensor(PIN_CLOSE_SENSOR, onDoorContactStateChange);
Relay garageDoorRelay(PIN_ACTIVATE, NULL, "GARAGE_DOOR");
#ifdef CG_MODEL_2
    DoorContact openSensor2(PIN_OPEN_SENSOR_2, NULL);
    DoorContact closeSensor2(PIN_CLOSE_SENSOR_2, NULL);
    Relay garageDoorRelay2(PIN_ACTIVATE_2, NULL, "GARAGE_DOOR_2");
#endif
LED sensorLED(PIN_SENSOR_LED, NULL);
LED wifiLED(PIN_WIFI_LED, NULL);
Task tCheckWifi(CHECK_WIFI_INTERVAL, TASK_FOREVER, &onCheckWiFi);
Task tCheckActivation(ACTIVATION_DURATION, TASK_FOREVER, &onCheckActivation);
Task tCheckMqtt(CHECK_MQTT_INTERVAL, TASK_FOREVER, &onCheckMqtt);
Task tSyncClock(CLOCK_SYNC_INTERVAL, TASK_FOREVER, &onSyncClock);
Task tEnableMqtt(MQTT_STARTUP_DELAY, TASK_ONCE, &onEnableMqtt);
Scheduler taskMan;
config_t config;
String lastState = "";
#ifdef CG_MODEL_2
    String lastState2 = "";
#endif
bool filesystemMounted = false;
volatile SystemState sysState = SystemState::BOOTING;
volatile bool ignoreMqtt = true;

/**
 * @brief Read the specified sensor pins and determine the door state. Prints
 * the result to console and returns the state as string.
 * @return The state string.
 */
String deviceStatus() {
    String state = "AJAR";
    if (openSensor.isOpen()) {
        state = "OPEN";
    }
    else if (closeSensor.isOpen()) {
        state = "CLOSED";
    }

    Serial.print(F("INFO: Door status = "));
    Serial.println(state);
    return state;
}

/**
 * @brief (Model 2 controllers only) Reads the door sensor to determine the
 * door state for door 2.
 */
#ifdef CG_MODEL_2
String deviceStatus2() {
    String state = "AJAR";
    if (openSensor2.isOpen()) {
        state = "OPEN";
    }
    else if (closeSensor2.isOpen()) {
        state = "CLOSED";
    }

    Serial.print(F("INFO: Door status = "));
    Serial.println(state);
    return state;
}
#endif

/**
 * @brief Gets the current time as a string.
 * @return String The current date/time.
 */
String getCurrentTime() {
    time_t now = time(nullptr);
    struct tm *timeinfo = localtime(&now);
    return String(asctime(timeinfo));
}

/**
 * @brief Synchronize the local system clock via NTP. Note: This does not take DST
 * into account. Currently, you will have to adjust the CLOCK_TIMEZONE define
 * manually to account for DST when needed.
 */
void onSyncClock() {
    configTime(TZ_America_New_York, "pool.ntp.org");

    Serial.print("INIT: Waiting for NTP time sync...");
    delay(500);
    while (!time(nullptr)) {
        ESPCrashMonitor.iAmAlive();
        Serial.print(F("."));
        delay(500);
    }
    
    Serial.println(F(" DONE"));
    Serial.print(F("INFO: Current time: "));
    Serial.println(getCurrentTime());
}

/**
 * @brief Enables MQTT message processing.
 */
void onEnableMqtt() {
    Serial.println(F("INIT: Disabling MQTT message processing deferral flag."));
    ignoreMqtt = false;
}

/**
 * @brief Publishes the system state to the MQTT status topic and
 * blinks the WiFi status LED.
 */
void publishSystemState() {
    if (mqttClient.connected()) {
        wifiLED.on();

        DynamicJsonDocument doc(200);
        doc["client_id"] = config.hostname;
        #ifdef CG_MODEL_2
            doc["door1State"] = deviceStatus();
            doc["door2State"] = deviceStatus2();
        #else
            doc["doorState"] = deviceStatus();
        #endif
        doc["firmwareVersion"] = FIRMWARE_VERSION;
        doc["systemState"] = (uint8_t)sysState;

        String jsonStr;
        size_t len = serializeJson(doc, jsonStr);
        Serial.print(F("INFO: Publishing system state: "));
        Serial.println(jsonStr);
        if (!mqttClient.publish(config.mqttTopicStatus.c_str(), jsonStr.c_str(), len)) {
            Serial.println(F("ERROR: Failed to publish message."));
        }

        doc.clear();
        wifiLED.off();
    }
}

/**
 * @brief Publishes a discovery packet to the configured discovery topic if
 * currently connected to WiFi.
 */
void publishDiscoveryPacket() {
    if (mqttClient.connected()) {
        wifiLED.on();

        DynamicJsonDocument doc(250);
        doc["name"] = config.hostname;
        doc["class"] = DEVICE_CLASS;
        doc["statusTopic"] = config.mqttTopicStatus;
        doc["controlTopic"] = config.mqttTopicControl;

        String jsonStr;
        size_t len = serializeJson(doc, jsonStr);
        Serial.print(F("INFO: Publishing discovery packet: "));
        Serial.println(jsonStr);
        if (!mqttClient.publish(config.mqttTopicStatus.c_str(), jsonStr.c_str(), len)) {
            Serial.println(F("ERROR: Failed to publish message."));
        }

        doc.clear();
        wifiLED.off();
    }
}

/**
 * @brief Resume normal operation. This will resume any suspended tasks.
 */
void resumeNormal() {
    Serial.println(F("INFO: Resuming normal operation..."));
    taskMan.enableAll();
    wifiLED.off();
    sysState = SystemState::NORMAL;
    publishSystemState();
}

/**
 * @brief Prints network information details to the serial console.
 */
void printNetworkInfo() {
    Serial.print(F("INFO: Local IP: "));
    Serial.println(WiFi.localIP());
    Serial.print(F("INFO: Gateway: "));
    Serial.println(WiFi.gatewayIP());
    Serial.print(F("INFO: Subnet mask: "));
    Serial.println(WiFi.subnetMask());
    Serial.print(F("INFO: DNS server: "));
    Serial.println(WiFi.dnsIP());
    Serial.print(F("INFO: MAC address: "));
    Serial.println(WiFi.macAddress());
    WiFi.printDiag(Serial);
}

/**
 * @brief Scan for available networks and dump each discovered network to the
 * console.
 */
void getAvailableNetworks() {
    ESPCrashMonitor.defer();
    Serial.println(F("INFO: Scanning WiFi networks..."));
    int numNetworks = WiFi.scanNetworks();
    for (int i = 0; i < numNetworks; i++) {
        Serial.print(F("ID: "));
        Serial.print(i);
        Serial.print(F("\tNetwork name: "));
        Serial.print(WiFi.SSID(i));
        Serial.print(F("\tSignal strength:"));
        Serial.println(WiFi.RSSI(i));
    }
    Serial.println(F("----------------------------------"));
}

/**
 * @brief Reboots the MCU after a 1 second delay.
 */
void reboot() {
    Serial.println(F("INFO: Rebooting... "));
    Serial.flush();
    delay(1000);
    ResetManager.softReset();
}

/**
 * @brief Stores the in-memory configuration to a JSON file stored in SPIFFS.
 * If the file does not yet exist, it will be created (see CONFIG_FILE_PATH).
 * Errors will be reported to the serial console if the filesystem is not
 * mounted or if the file could not be opened for writing.
 */
void saveConfiguration() {
    Serial.print(F("INFO: Saving configuration to: "));
    Serial.print(CONFIG_FILE_PATH);
    Serial.println(F(" ... "));
    if (!filesystemMounted) {
        Serial.println(F("FAIL"));
        Serial.println(F("ERROR: Filesystem not mounted."));
        return;
    }

    StaticJsonDocument<350> doc;
    doc["hostname"] = config.hostname;
    doc["useDHCP"] = config.useDhcp;
    doc["ip"] = config.ip.toString();
    doc["gateway"] = config.gw.toString();
    doc["subnetMask"] = config.sm.toString();
    doc["dnsServer"] = config.dns.toString();
    doc["wifiSSID"] = config.ssid;
    doc["wifiPassword"] = config.password;
    doc["mqttBroker"] = config.mqttBroker;
    doc["mqttPort"] = config.mqttPort;
    doc["mqttControlTopic"] = config.mqttTopicControl;
    doc["mqttStatusTopic"] = config.mqttTopicStatus;
    doc["mqttDiscoveryTopic"] = config.mqttTopicDiscovery;
    doc["mqttUsername"] = config.mqttUsername;
    doc["mqttPassword"] = config.mqttPassword;
    #ifdef ENABLE_OTA
        doc["otaPort"] = config.otaPort;
        doc["otaPassword"] = config.otaPassword;
    #endif

    File configFile = SPIFFS.open(CONFIG_FILE_PATH, "w");
    if (!configFile) {
        Serial.println(F("FAIL"));
        Serial.println(F("ERROR: Failed to open config file for writing."));
        doc.clear();
        return;
    }

    serializeJsonPretty(doc, configFile);
    doc.clear();
    configFile.flush();
    configFile.close();
    Serial.println(F("DONE"));
}

/**
 * @brief Helper method for printing a warning message during config load.
 * @param message The message to print.
 */
void printWarningAndContinue(const __FlashStringHelper *message) {
    Serial.println();
    Serial.println(message);
    Serial.print(F("INFO: Continuing... "));
}

/**
 * @brief Sets the running config to default configuration values.
 */
void setConfigurationDefaults() {
    String chipId = String(ESP.getChipId(), HEX);
    String defHostname = String(DEVICE_NAME) + "_" + chipId;

    config.hostname = defHostname;
    config.ip = defaultIp;
    config.mqttBroker = MQTT_BROKER;
    config.mqttPassword = "";
    config.mqttPort = MQTT_PORT;
    config.mqttTopicControl = MQTT_TOPIC_CONTROL;
    config.mqttTopicStatus = MQTT_TOPIC_STATUS;
    config.mqttTopicDiscovery = MQTT_TOPIC_DISCOVERY;
    config.mqttUsername = "";
    config.password = DEFAULT_PASSWORD;
    config.sm = defaultSm;
    config.ssid = DEFAULT_SSID;
    config.useDhcp = false;
    config.clockTimezone = CLOCK_TIMEZONE;
    config.dns = defaultDns;
    config.gw = defaultGw;

    #ifdef ENABLE_OTA
        config.otaPassword = OTA_PASSWORD;
        config.otaPort = OTA_HOST_PORT;
    #endif
}

/**
 * @brief Loads the configuration from CONFIG_FILE_PATH into memory and uses that as
 * the running configuration. Will report errors to the serial console and
 * revert to the default configuration under the following conditions:
 * 1) The filesystem is not mounted.
 * 2) The config file does not exist in SPIFFS. In this case a new file
 * will be created and populated with the default configuration.
 * 3) The config file exists, but could not be opened for reading.
 * 4) The config file is too big ( > 1MB).
 * 5) The config file could not be deserialized to a JSON structure.
 */
void loadConfiguration() {
    memset(&config, 0, sizeof(config));

    Serial.print(F("INFO: Loading config file: "));
    Serial.print(CONFIG_FILE_PATH);
    Serial.print(F(" ... "));
    if (!filesystemMounted) {
        Serial.println(F("FAIL"));
        Serial.println(F("ERROR: Filesystem not mounted."));
        return;
    }

    if (!SPIFFS.exists(CONFIG_FILE_PATH)) {
        Serial.println(F("FAIL"));
        Serial.println(F("WARN: Config file does not exist. Creating with default config..."));
        saveConfiguration();
        return;
    }

    File configFile = SPIFFS.open(CONFIG_FILE_PATH, "r");
    if (!configFile) {
        Serial.println(F("FAIL"));
        Serial.println(F("ERROR: Unable to open config file. Using default config."));
        return;
    }

    size_t size = configFile.size();
    uint16_t freeMem = ESP.getMaxFreeBlockSize() - 512;
    if (size > freeMem) {
        Serial.println(F("FAIL"));
        Serial.print(F("ERROR: Not enough free memory to load document. Size = "));
        Serial.print(size);
        Serial.print(F(", Free = "));
        Serial.println(freeMem);
        configFile.close();
        return;
    }

    DynamicJsonDocument doc(freeMem);
    DeserializationError error = deserializeJson(doc, configFile);
    if (error) {
        Serial.println(F("FAIL"));
        Serial.println(F("ERROR: Failed to parse config file to JSON. Using default config."));
        configFile.close();
        return;
    }

    doc.shrinkToFit();
    configFile.close();

    String chipId = String(ESP.getChipId(), HEX);
    String defHostname = String(DEVICE_NAME) + "_" + chipId;

    config.hostname = doc.containsKey("hostname") ? doc["hostname"].as<String>() : defHostname;
    config.useDhcp = doc.containsKey("useDhcp") ? doc["useDhcp"].as<bool>() : false;
    if (doc.containsKey("ip")) {
        if (!config.ip.fromString(doc["ip"].as<String>())) {
            printWarningAndContinue(F("WARN: Invalid IP in configuration. Falling back to factory default."));
        }
    }
    else {
        config.ip = defaultIp;
    }
    
    if (doc.containsKey("gateway")) {
        if (!config.gw.fromString(doc["gateway"].as<String>())) {
            printWarningAndContinue(F("WARN: Invalid gateway in configuration. Falling back to factory default."));
        }
    }
    else {
        config.gw = defaultGw;
    }
    
    if (doc.containsKey("subnetmask")) {
        if (!config.sm.fromString(doc["subnetMask"].as<String>())) {
            printWarningAndContinue(F("WARN: Invalid subnet mask in configuration. Falling back to default."));
        }
    }
    else {
        config.sm = defaultSm;
    }

    if (doc.containsKey("dns")) {
        if (!config.dns.fromString(doc["dnsServer"].as<String>())) {
            printWarningAndContinue(F("WARN: Invalid DSN server in configuration. Falling back to default."));
        }
    }
    else {
        config.dns = defaultDns;
    }
    
    config.ssid = doc.containsKey("wifiSSID") ? doc["wifiSSID"].as<String>() : DEFAULT_SSID;
    config.password = doc.containsKey("wifiPassword") ? doc["wifiPassword"].as<String>() : DEFAULT_PASSWORD;
    config.mqttBroker = doc.containsKey("mqttBroker") ? doc["mqttBroker"].as<String>() : MQTT_BROKER;
    config.mqttPort = doc.containsKey("mqttPort") ? doc["mqttPort"].as<int>() : MQTT_PORT;
    config.mqttTopicControl = doc.containsKey("mqttControlTopic") ? doc["mqttControlTopic"].as<String>() : MQTT_TOPIC_CONTROL;
    config.mqttTopicStatus = doc.containsKey("mqttStatusTopic") ? doc["mqttStatusTopic"].as<String>() : MQTT_TOPIC_STATUS;
    config.mqttTopicDiscovery = doc.containsKey("mqttDiscoveryTopic") ? doc["mqttDiscoveryTopic"].as<String>() : MQTT_TOPIC_DISCOVERY;
    config.mqttUsername = doc.containsKey("mqttUsername") ? doc["mqttUsername"].as<String>() : "";
    config.mqttPassword = doc.containsKey("mqttPassword") ? doc["mqttPassword"].as<String>() : "";
    #ifdef ENABLE_OTA
        config.otaPort = doc.containsKey("otaPort") ? doc["otaPort"].as<uint16_t>() : MQTT_PORT;
        config.otaPassword = doc.containsKey("otaPassword") ? doc["otaPassword"].as<String>() : OTA_PASSWORD;
    #endif

    doc.clear();
    Serial.println(F("DONE"));
}

/**
 * @brief Confirms with the user that they wish to do a factory restore. If so, then
 * clears the current configuration file in SPIFFS, then reboots. Upon reboot,
 * a new config file will be generated with default values.
 */
void doFactoryRestore() {
    Serial.println();
    Serial.println(F("Are you sure you wish to restore to factory default? (Y/n)?"));
    Console.waitForUserInput();

    String str = Console.getInputString();
    if (str == "Y" || str == "y") {
        Serial.print(F("INFO: Clearing current config... "));
        if (filesystemMounted) {
            if (SPIFFS.remove(CONFIG_FILE_PATH)) {
                Serial.println(F("DONE"));
                Serial.print(F("INFO: Removed file: "));
                Serial.println(CONFIG_FILE_PATH);

                Serial.print(F("INFO: Rebooting in "));
                for (uint8_t i = 5; i >= 1; i--) {
                    Serial.print(i);
                    Serial.print(F(" "));
                    delay(1000);
                }

                reboot();
            }
            else {
                Serial.println(F("FAIL"));
                Serial.println(F("ERROR: Failed to delete configuration file."));
            }
        }
        else {
            Serial.println(F("FAIL"));
            Serial.println(F("ERROR: Filesystem not mounted."));
        }
    }

    Serial.println();
}

/**
 * @brief Attempts to re-connect to the MQTT broker if then connection is
 * currently broken.
 * @return true if a connection to the MQTT broker is either already
 * established, or was successfully re-established; Otherwise, false.
 * If the connection is re-established, then will also re-subscribe to
 * the status channel.
 */
bool reconnectMqttClient() {
    if (!mqttClient.connected()) {
        Serial.print(F("INFO: Attempting to establish MQTT connection to "));
        Serial.print(config.mqttBroker);
        Serial.print(F(" on port: "));
        Serial.print(config.mqttPort);
        Serial.println(F("..."));
        
        bool didConnect = false;
        if (config.mqttUsername.length() > 0 && config.mqttPassword.length() > 0) {
            didConnect = mqttClient.connect(config.hostname.c_str(), config.mqttUsername.c_str(), config.mqttPassword.c_str());
        }
        else {
            didConnect = mqttClient.connect(config.hostname.c_str());
        }

        if (didConnect) {
            Serial.print(F("INFO: Subscribing to topic: "));
            Serial.println(config.mqttTopicControl);
            mqttClient.subscribe(config.mqttTopicControl.c_str());

            Serial.print(F("INFO: Publishing to topic: "));
            Serial.println(config.mqttTopicStatus);

            Serial.print(F("INFO: Discovery topic: "));
            Serial.println(config.mqttTopicDiscovery);
        }
        else {
            String failReason = TelemetryHelper::getMqttStateDesc(mqttClient.state());
            Serial.print(F("ERROR: Failed to connect to MQTT broker: "));
            Serial.println(failReason);
            return false;
        }
    }

    return true;
}

/**
 * @brief Callback method for checking the MQTT connection state and
 * reconnecting if necessary. If the connection is broken, and
 * reconnection fails, another attempt will be made after CHECK_MQTT_INTERVAL.
 */
void onCheckMqtt() {
    Serial.println(F("INFO: Checking MQTT connection status..."));
    if (reconnectMqttClient()) {
        Serial.println(F("INFO: Successfully reconnected to MQTT broker."));
        publishSystemState();
        publishDiscoveryPacket();
    }
    else {
        Serial.println(F("ERROR: MQTT connection lost and reconnect failed."));
        Serial.print(F("INFO: Retrying connection in "));
        Serial.print(CHECK_MQTT_INTERVAL % 1000);
        Serial.println(F(" seconds."));
    }
}

/**
 * @brief Activates the door control relay, sends response to HTTP client, and
 * blinks WiFi LED to indicate activity.
 */
void activateDoor() {
    Serial.print(F("INFO: Activating door "));
    #ifdef CG_MODEL_2
        Serial.print(F(" 1 "));
    #endif
    Serial.print(F("@ "));
    Serial.println(getCurrentTime());
    wifiLED.on();
    garageDoorRelay.close();
    publishSystemState();
    wifiLED.off();
}

#ifdef CG_MODEL_2
void activateDoor2() {
    Serial.print(F("INFO: Activating door 2 @ "));
    Serial.println(getCurrentTime());
    wifiLED.on();
    garageDoorRelay2.close();
    publishSystemState();
    wifiLED.off();
}
#endif
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
void loop() {
    ESPCrashMonitor.iAmAlive();
    Console.checkInterrupt();
    taskMan.execute();
    #ifdef ENABLE_MDNS
        mdns.update();
    #endif
    #ifdef ENABLE_OTA
        ArduinoOTA.handle();
    #endif
    mqttClient.loop();
}

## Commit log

2019-06-03 Adding crash monitor and disassembly support
    [main.cpp]
2019-07-09 Adding schematics and BOM.
    [CyGarage.fzz]
2019-07-09 Fixup schematics
    [CyGarage.fzz]
2019-07-09 Fix schematic labels
    [CyGarage.fzz]
2019-07-29 Adding ability to save/load configuration settings
    Also fixing duplicate notifications sent from openhab rules.
    [main.cpp]
2019-07-29 Fix hostname and webserver port config
    [main.cpp]
2019-08-05 Adding input isolation to the circuit
    Also added integration documentation
    [CyGarage.fzz]
2019-08-06 Bumping PCB board revision
    [CyGarage.fzz]
2019-09-05 Fixing openhab rules, separating bridge from bindings, DNS.
    [main.cpp]
2019-10-29 Updating board version (OSHW)
    [CyGarage.fzz]
2019-11-07 Adding gerber files
    [CyGarage_contour.gm1, CyGarage_copperBottom.gbl, CyGarage_copperTop.gtl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]
2019-11-12 Change holes to M3 and add text
    [CyGarage.fzz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]
2019-11-13 Update PCB and re-export gerber files for fab
    [CyGarage.fzz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]
2019-11-22 Update for model 2 (2-door version)
    [CyGarage-Model2.fzz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]
2020-06-15 Don't block boot on WiFi fail. Move CLI to lib.
    [Console.cpp, config.h, main.cpp]
2020-12-05 Fixing door auto-opening on start-up
    [main.cpp]
2020-12-05 Friends don't let friends use Autorouter.
    [CyGarage-Model2.fzz, CyGarage.fzz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]
2022-08-25 Hardware redesign, doc updates, better sens check
    [BOM_CyGarage.csv, BOM_PCB_CyGarageM2.csv, CyGarage-Model2.fzz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]
